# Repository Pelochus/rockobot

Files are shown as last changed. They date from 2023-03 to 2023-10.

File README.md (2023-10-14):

# Rockobot
Battlebot made for SMP subject in Computer Engineering, UGR. This subject focuses on learning microcontrollers and embedded systems, with Arduino especifically. In order to properly learn an actual use case for embedded systems, we have to build a battlebot and make it compete with our classmates' counterparts in a tournament. Personally, we wanted to take the chance to learn a bit more of what was taught in class, so we learned both Fusion 360 and KiCad in order to improve the performance and originality of our robot, adding custom 3D printed parts and a self-designed PCB. Here we have a photo of the final assembly:

RockobotV1

This repository contains information about the mechanics, electronics and programming of the robot along with parts lists, tools used, future ideas and a knowledge database. This README serves as an index for each subsection (Mechanics/Printables, Electronics and Programming) and for some generic stuff. For detailed information, see the READMEs for each subsection:

- [Mechanics/3D Printables](https://github.com/Pelochus/rockobot/tree/main/printables/)
- [Electronics](https://github.com/Pelochus/rockobot/tree/main/electronics/)
- [Arduino/Software](https://github.com/Pelochus/rockobot/tree/main/arduino/)

## Arduino Blog
We were featured in the official Arduino blog! Check this [link](https://blog.arduino.cc/2023/09/29/can-you-smell-what-the-rockobot-is-cooking/)!

## Tournament Results
**Rockobot won 5 matches and tied one!**. Our battlebot achieved the best result of our class, essentially winning the tournament (there were 17 robots including ours, but each one only had to participate in 6 matches). Additionally, we got a 10/10 from our classmates votes. The final mark for Rockobot was a 9.92 out of 10. Here is a video of the full competition:

[Robots Tournament 2023 - SMP UGR](https://www.youtube.com/watch?v=Jcgc2-T2o4o)

# Index
### Mechanics/3D Printables

1. [Components](https://github.com/Pelochus/rockobot/tree/main/printables#Components)
2. [Tools](https://github.com/Pelochus/rockobot/tree/main/printables#Tools)
3. [Requirements](https://github.com/Pelochus/rockobot/tree/main/printables#Requirements)
4. [3D designs](https://github.com/Pelochus/rockobot/tree/main/printables#3D-designs)
5. [Enhancing 3D prints strength](https://github.com/Pelochus/rockobot/tree/main/printables#Enhancing-3D-prints-strength)
6. [Mechanical designs](https://github.com/Pelochus/rockobot/tree/main/printables#Mechanical-designs)
7. [Ideas](https://github.com/Pelochus/rockobot/tree/main/printables#Ideas)
8. [Knowledge Base](https://github.com/Pelochus/rockobot/tree/main/printables#Knowledge-base)

### Electronics

1. [Components](https://github.com/Pelochus/rockobot/tree/main/electronics#Components)
2. [Tools](https://github.com/Pelochus/rockobot/tree/main/electronics#Tools)
3. [PCB](https://github.com/Pelochus/rockobot/tree/main/electronics#PCB)
4. [Circuits](https://github.com/Pelochus/rockobot/tree/main/electronics#Circuits)
5. [Ideas](https://github.com/Pelochus/rockobot/tree/main/electronics#Ideas)
6. [Knowledge Base](https://github.com/Pelochus/rockobot/tree/main/electronics#Knowledge-base)

### Arduino/Software

1. [Components](https://github.com/Pelochus/rockobot/tree/main/arduino#Components)
2. [Tools](https://github.com/Pelochus/rockobot/tree/main/arduino#Tools)
3. [Functions](https://github.com/Pelochus/rockobot/tree/main/arduino#Functions)
4. [Reducing the number of digital pins](https://github.com/Pelochus/rockobot/tree/main/arduino#Reducing-the-number-of-digital-pins)
5. [Ideas](https://github.com/Pelochus/rockobot/tree/main/arduino#Ideas)
6. [Knowledge Base](https://github.com/Pelochus/rockobot/tree/main/arduino#Knowledge-base)

## Why the name Rockobot?
As you can see, Rockobot has Dwayne "The Rock" Johnson head in it. The reason behind this was due to the 3D printing community having a weird obsession with putting The Rock's head on everything they printed and, since we both knew that, we joined our fellow 3D printing enthusiasts in adding The Rock's head everywhere.

## TODO
- Everything is finished! Only need to do a improved version

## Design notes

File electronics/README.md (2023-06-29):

# Electronics 
This section will focus on the electronics side of Rockobot

## Components
| Component | Units | Notes | Link |
| --- | ----- | --- | --- |
| Soldering Tin | - | | - |
| Wires | - | Dupont or common wires | - |
| 5K Ohms Resistors | 4 | Used with infrarred sensors | - |
| 100 Ohms Resistors | 4 | Used with infrarred sensors | - |
| Metallic Power Button | 1 | Red, with LEDs | https://es.aliexpress.com/item/1005004917197015.html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 |
| RCWL-1601 US Sensor | 2 | Very similar to HC-SR04 | https://es.aliexpress.com/item/1005001622236950.html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 |
| TCRT5000 Reflect IR | 4 | | https://es.aliexpress.com/item/32841920225.html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 |
| JGA25-370 DC Motor | 2 | 100RPM@12V **Not used** | |
| L289N Motor Driver | 1 | | https://es.aliexpress.com/item/33012645746.html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 |
| StepDown Converter 5V | 2 | One at ~8V the other at ~5V | https://es.aliexpress.com/item/1005003709975604.html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 |
| 1550mAh 14.8V Battery | 1 | 4S LiPo, with XT60 connector  | https://www.amazon.es/Tattu-Batería-Multicopteros-Helicópteros-diversos/dp/B016Q3QT2W/ref=sr_1_6?__mk_es_ES=ÅMÅŽÕÑ&crid=17YJJHHE4X53W&keywords=bateria+4s+lipo&qid=1688040709&sprefix=bateria+4s+lipo+%2Caps%2C218&sr=8-6 |
| Battery Alarm | 1 | | https://es.aliexpress.com/item/1005003884877902.html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 |
| XT-60 Female | 1 | Used for battery connection | https://es.aliexpress.com/item/32832063718.html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 |
| JSTXH2.54 4P Wire | 6 | For sensors/motors connection | https://es.aliexpress.com/item/32954418743.html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 |
| JSTXH2.54 4P Female | 6 | For sensors/motors connection | Link above |
| Male 2.54 Pins | ~20 | For some connections/upgrades | https://es.aliexpress.com/item/32864964634.html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 |
| Rockobot v1.0 PCB | 1 | | |
| Optional Components | - | Some other useful components: | Heat Shrink tubing, insulating tape... |

## Tools
- Soldering Iron
- Balance Charger

## PCB
Here we have a photo of the PCB in KiCad:

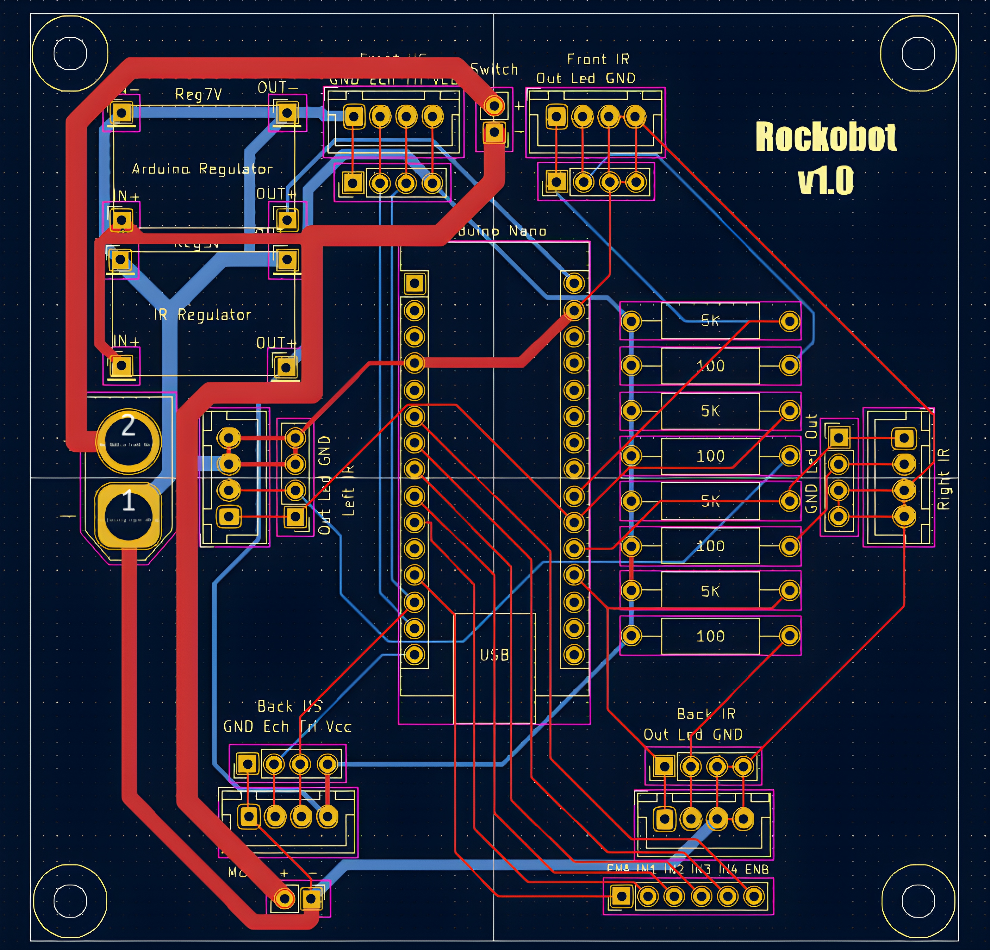
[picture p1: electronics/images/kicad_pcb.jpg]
KiCadPCB


We can see these components:
- Various connectors, including male 2.54 pins, JSTXH 2.54 for the sensors and XT60 male for the battery
- Resistors for the IR sensors
- 2 voltage regulators, one will be exclusively for the Arduino (needs more than 7V, max 12V, the Vin pin will do the rest) and the other for the sensors (both infrarred and US) at 5 volts
- Arduino NANO itself

The final result should look like this (except for all the male pins which are connected to the JST, which are **backup connectors**):

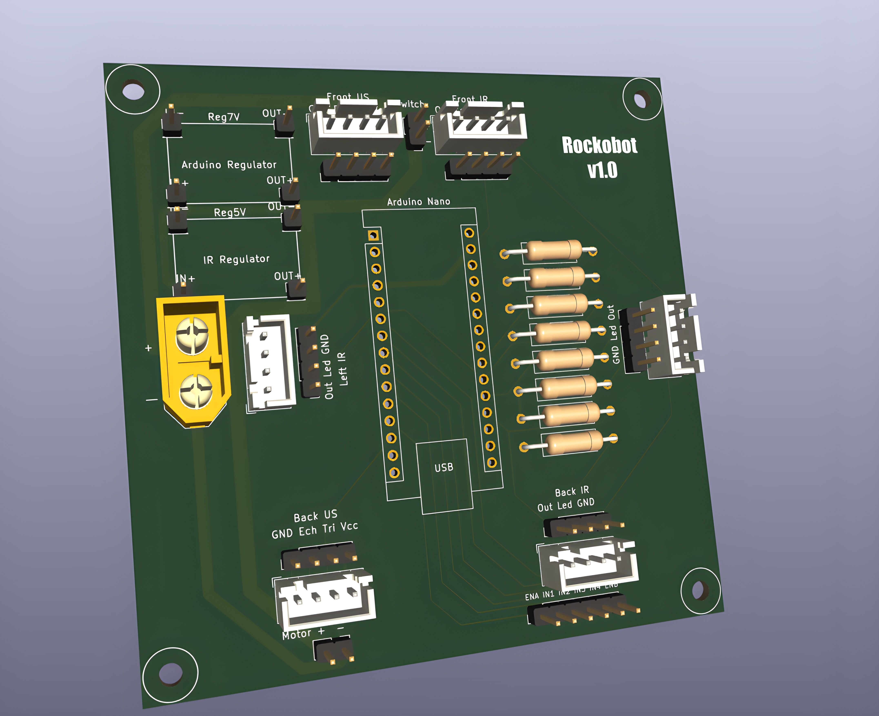
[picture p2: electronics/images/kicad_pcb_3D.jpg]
KiCadPCB3D


However we made little changes to adapt it to our final design. The only two important changes are **the female pins for the Arduino** (so we can remove it or insert it whenever we want) and the **position of the XT60 connector**, which is facing downwards because our battery didn't have a long enough wire. We also did not include those extra male pins, which were inserted just in case we had problems with the JST connectors.

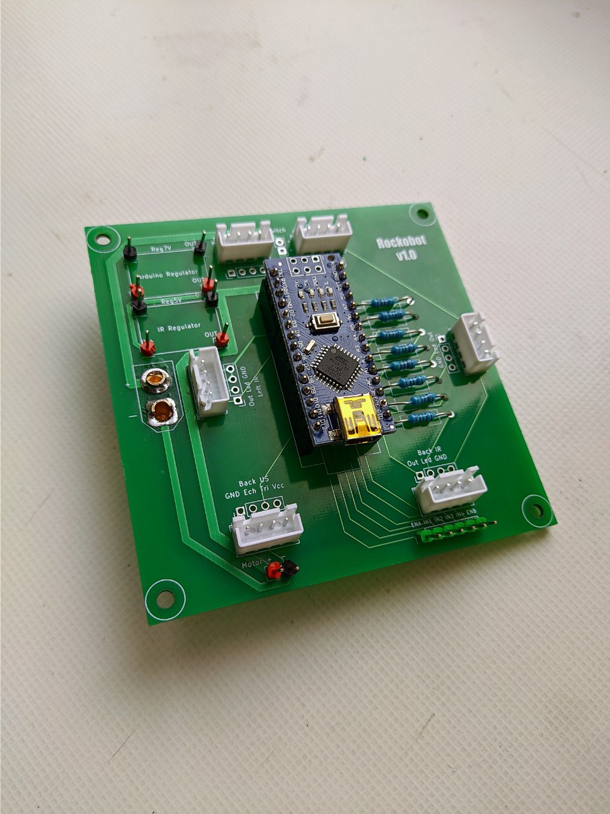
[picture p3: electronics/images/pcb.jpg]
PCB-Almost-Finished


Here is the totally finished design integrated in the robot (we used insulating tape to avoid unintended shortcircuits):

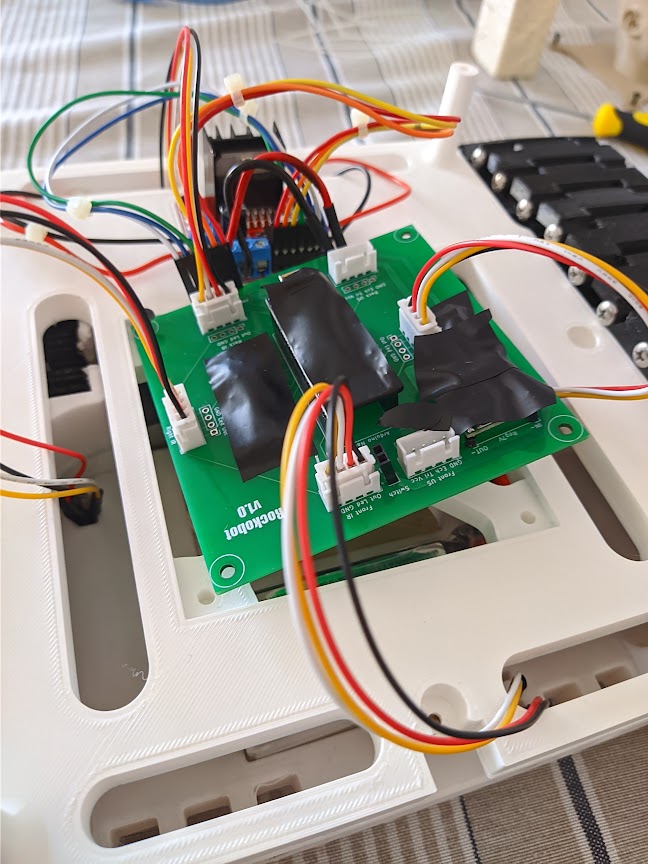
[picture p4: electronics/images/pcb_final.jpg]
PCB-Finished


## Circuits
This is a photo of the schematic:

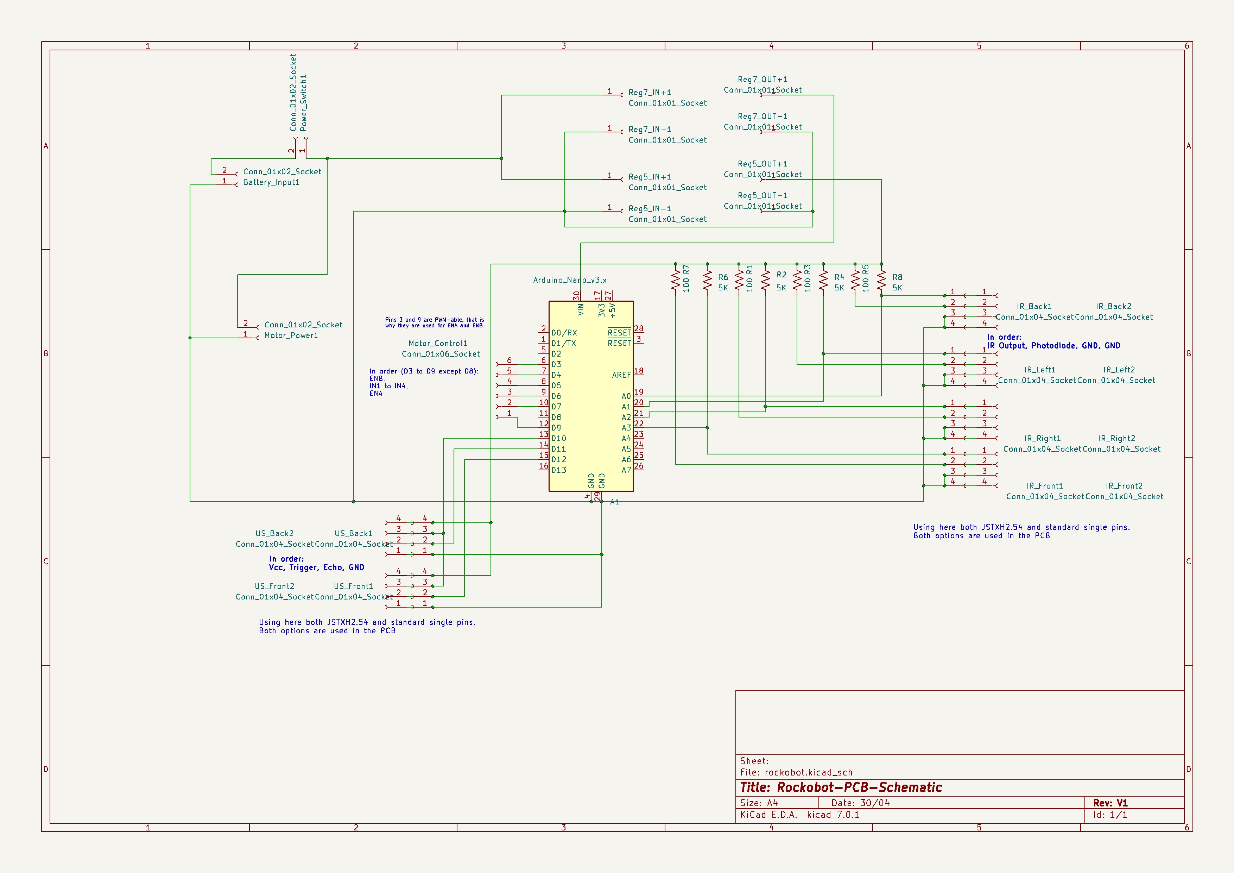
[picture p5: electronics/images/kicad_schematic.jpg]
KiCadSchematic


Essentially, the circuit does this:

Connection to battery -> Power Button -> Divide current in 3, one directly to the L298N driver, the other 2 to the voltage regulators -> One regulator will power the Arduino through V<sub>in</sub>, the other will power the sensors -> Connect Arduino and sensors/driver through digital pins and analog pins

## Ideas
Here are some ideas for future revisions:
- Change from Arduino NANO to, for example, ESP32
- Add a section to the PCB with male pins connected to the digital pins, to add some modularity. Also add two more male pins, one connected to Arduino 5V and the other to GND
- Change some pins (like the 6 motor driver pins) to other JST XH2.54 or other connectors. For the previous example, from common male pins to JST XH2.54 6P
- Rethink some components like the regulators. For example:
  - Reduce to just one regulator, by using the Arduino for powering sensors (depending on how many sensors are used, in this design it is possible but near the Arduino limit)
  - Change to a fixed SMD regulator, to avoid changing the potentiometer unintentionally to an unsafe voltage. Also to better fit in the PCB (current implementation is rather messy)
- Resize PCB accordingly to what new changes were introduced

## Knowledge Base
- [KiCad 7 Tutorial, from schematics to final PCB](https://www.youtube.com/watch?v=3FGNw28xBr0)

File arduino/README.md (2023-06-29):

# Software
This section will focus on the software side of Rockobot

## Components
- Arduino NANO V3 or clone. We used Elegoo NANO V3

## Tools
- Computer
- Mini USB-B to USB-A/USB-C
- Arduino IDE

## Functions
The majority of functions here are very simple, except for the main function that decides what to do. There is information about the library for controlling the motor driver [here](https://github.com/Pelochus/rockobot/blob/main/arduino/libraries/l298n-rockobot/README.md). Let's take a look at the main function of Rockobot:
```c++
void rockobot_think() {
  extra_delay = 800; // Add an extra delay when encountering black lines

  ////////////////
  // Read Sensors
  ////////////////
  uint8_t front_distance = us_front.measureDistanceCm();
  uint8_t back_distance = us_back.measureDistanceCm();
  bool ir_front = (analogRead(IR_FRONT) > IR_THRESHOLD);
  bool ir_back = (analogRead(IR_BACK) > IR_THRESHOLD);
  bool ir_right = (analogRead(IR_RIGHT) > IR_THRESHOLD);
  bool ir_left = (analogRead(IR_LEFT) > IR_THRESHOLD);

  /////////
  // Think
  /////////
  uint8_t speed = 100;
  direction_t direction = driver.get_direction(); // Maintain same path while thinking

  // Anti-ramp
  if ((ir_front ? 1 : 0) + (ir_back ? 1 : 0) +
      (ir_right ? 1 : 0) + (ir_left ? 1 : 0) > 2) {
    direction = RIGHT;
  }
  else if (ir_front) {
    direction = BACKWARD;
  }

  /**
   * Rest of IR ifs
   */

  // We want even higher delays on rotations, because robot is slower with only one motor
  else if (ir_right) {
    extra_delay += 200;
    direction = WIDE_LEFT;
  }
  else {
    ///////////////////////////////////////////////////////
    // Not in danger zone, search and target enemy with US
    ///////////////////////////////////////////////////////
    extra_delay = 0; // Reset delay if not in danger
    speed = 80;

    int16_t us_diff = front_distance - back_distance; // If negative, back_distance is farther from something and viceversa
    uint8_t us_min = (front_distance < back_distance) ? front_distance : back_distance;
    bool search = us_min > US_NEARBY_ENEMY; // Decide whether to skip or not search stage

    //////////
    // Search
    //////////

    if (search) {
      switch (search_stage) {
        case 0 ... (TURN_CYCLES - 1):
          direction = RIGHT;
          break;
        case 2 * TURN_CYCLES ... (3 * TURN_CYCLES):
          direction = LEFT;
          break;
        default:
          direction = FORWARD;
      }

      search_stage++;
      search_stage %= 4 * TURN_CYCLES;
    }

    ////////////////
    // Target enemy
    ////////////////

    if (abs(us_diff) > DIRECTION_CHANGE_THRESHOLD && us_min < US_NEARBY_ENEMY) {
      if (us_diff > 0) direction = BACKWARD;
      else if (us_diff < 0) direction = FORWARD;
      // else will retain current direction
    }

    // Activate max power if close enough
    if (us_min < FULL_POWER_NEAR_ENEMY) speed = 100;
  }

  //////////////////////
  // Act after thinking
  //////////////////////

  driver.set_speed_percentage(speed);
  driver.set_direction(direction);
}
```

As we can see, we can easily divide the function in 3 parts: **sense, think and act**

We have some extra functionality to the robot, like the ```extra_delay``` variable, which augments the delay between one loop and the following when encountering black lines. This way, we do not allow the robot to rethink actions very frequently while it is avoiding black lines, just escapes from the black lines. Some of this extra functionality is outside the main function and is implemented either on the ```void setup()``` or the ```void loop()```. For extra details on the main function, see [rockobot-main.ino](https://github.com/Pelochus/rockobot/blob/main/arduino/rockobot-main/rockobot-main.ino)

## Reducing the number of digital pins
Since an Arduino NANO only has 13 digital pins, controlling 2 US sensors, 4 infrarred sensors and 2 motors is almost impossible without using transistors or other methods of switching elements.
Luckily, since we have some redundancy, we can "compress" the number of pins used. First, let's see how many pins we need:

- **2 digital pins** for each ultrasonic sensor, so **4 in total**
- **1 digital pin** per infrarred sensor, **4 in total**
- **4 analogic pins**, 1 per infrarred sensor
- **6 digital pins** (2 must be PWM) for the motor driver

As we can see, **14 digital pins**, 1 more than what a Nano has. We reduced the pins the following way:

- **3 digital pins** for the US sensors, we used the same pin for the trigger pin of each one, since we will mostly reading both at once
- **0 digital pins** for the infrarred sensors, changed for 5V pin. This was necessary for the infrarred LED to be turned on or off, but we can keep it on indefinitely
- The driver **could be using 5 pins** (combine the digital pin used for PWM), but we will keep them separately just in case we want to have different speeds per motor

With this reduction, **we only use 9 digital pins**, having some spare digital pins in case we wanted to add, for example, bumpers or decorative LEDs.

## Ideas
- Switch between IR controlled mode and autonomous mode:
    - Wait for an input at setup with 2 buttons, one for each mode, in loop function, call either autonomous or controlled mode
    - Make the input a key, similar to a car

## Knowledge Base
- [Arduino Docs](https://docs.arduino.cc/)
- [UltraSonic Sensor Library](https://github.com/Martinsos/arduino-lib-hc-sr04)

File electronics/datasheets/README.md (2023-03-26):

# Datasheets
This subsections is of minor importance. Below some notes about the datasheets of the electronic components used

## Notes
- RCWL-1601 ultrasonic sensor is extremely similar to HC-SR04 counterpart but better. Almost everything is equal (even software) except for lower consumption (2 mA vs 8 mA) and this sensor is capable of 3.3V logic, making it a better choice for RPi and ESP32
- There is no specific datasheet for the 12V@100 RPM edition of the JGA25-370, so a partially complete datasheet + some PNGs from the store it was bought are included
- The step-down converter does not even have a specific part number. Similarly, some screenshots are included with information
- The red metallic button is also generic, so again some screenshots with some specs

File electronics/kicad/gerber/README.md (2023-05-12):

## Note about gerber files
Gerber files here are generated for JLCPCB according to their guide for KiCad 6/7. The .zip contains all files necessary for ordering

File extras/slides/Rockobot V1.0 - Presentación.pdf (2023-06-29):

# Rockobot V1.0

# Realizado por:

# Ángel Hurtado José Hinojosa

# Índice

## - Objetivos

## - Diseño 3D:

## - Estructura

## - Mecánica

## - Electrónica

## - Componentes

## - PCB

## - Programación

## - Problemas

# Objetivos

## Queríamos hacer un robot que cumpliese lo siguiente:

## - Fuerte y grande

## - Modular y reparable

## - Impreso en 3D en su mayoría

## - Usar Orugas (Tanque)

## - Circuitería ordenada

## - Programación simple

# Diseño 3D: Estructura

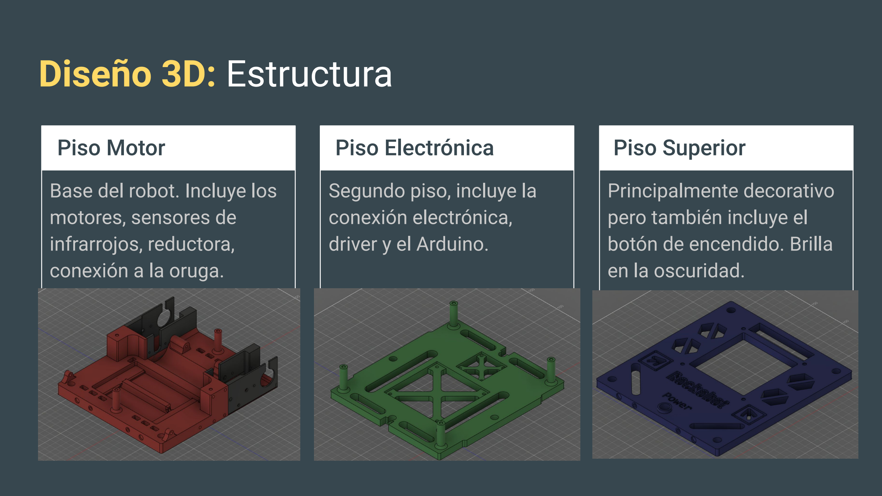
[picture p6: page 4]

## Piso Motor

### Base del robot. Incluye los motores, sensores de

infrarrojos, reductora,
conexión a la oruga.

## Piso Electrónica

### Segundo piso, incluye la

conexión electrónica,
driver y el Arduino.

## Piso Superior

### Principalmente decorativo pero también incluye el botón de encendido. Brilla

en la oscuridad.

# Diseño 3D: Estructura

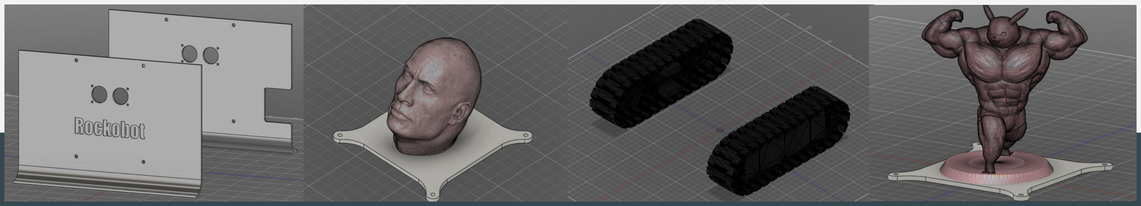
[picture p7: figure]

## Shields

Escudos de acero
inoxidable. Integran en
ellos unos agujeros para el sensor de ultrasonidos

## Rockins

Módulos para el piso
superior. Principalmente
decorativos, pero pueden
ser funcionales
(iluminación, por ejemplo)

## Tracks

4 piezas: Oruga de plástico flexible, frame para
conexión oruga-cuerpo y 2
tipos de engranajes: para
movimiento y para tensión

## Otros componentes

Para conexión de las
piezas se usaron tornillos, tuercas, threaded inserts, arandelas, silicona para
algunos apaños etc...

# Diseño 3D: Mecánica

## - 3 partes:

- Caja de engranajes
- Oruga con filamento flexible (TPU)
- Frame para la oruga y conexión con engranajes

## - Lubricación de engranajes con vaselina (el plástico para impresoras 3D lo prefiere a otros lubricantes) - Muchos tornillos (unos 120, 64 para la oruga) - Reducción de velocidad aproximadamente 86:1 (86 veces más lento, pero mayor par motor)

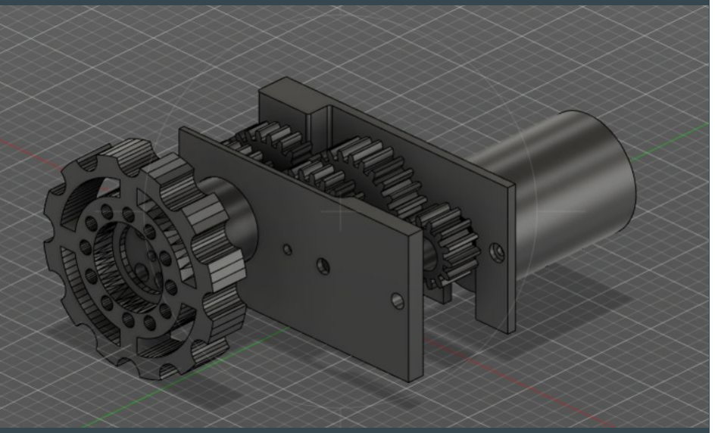
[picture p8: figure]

Gearbox, motor y engranaje principal, que engancha a la oruga flexible

# Construcción del diseño 3D

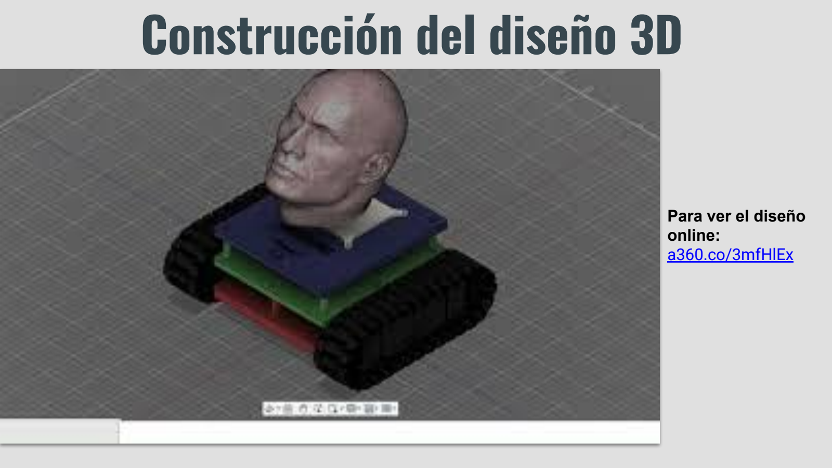
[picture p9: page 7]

Para ver el diseño
online:
a360.co/3mfHlEx

# Electrónica: Componentes

Componentes usados:

- Arduino NANO v3
- L298N motor driver
- RCWL-1601 US sensor x2
- TCRT5000 IR sensor x4
- Step-Down converter Mini 360 x2
- Batería de 14.8V y 1550 mAh
- Alarma para batería baja
- Motores de un VHS antiguo x2
- Rockobot V1.0 PCB
- Botón guay de Aliexpress
- Conector XT-60 (para batería)
- Conectores y cables JSTXH2.5, para los sensores
- Resistencias, cables, estaño…

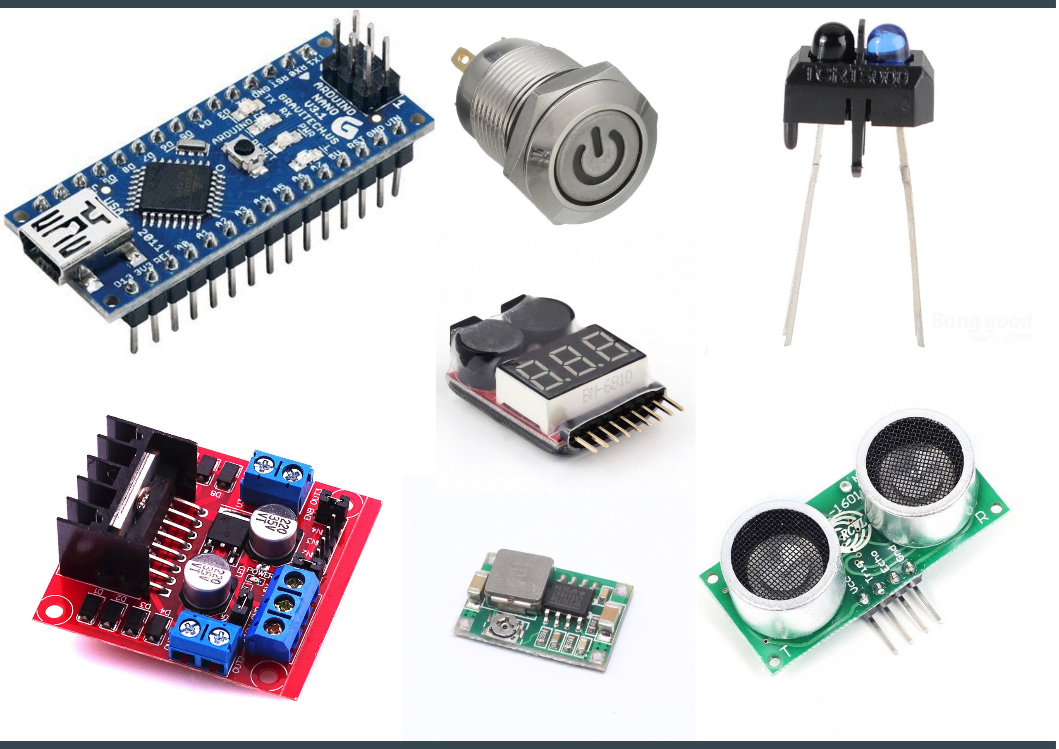
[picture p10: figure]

Electrónica: Componentes | Esquema electrónico del
robot. Se divide tal que: - Entrada de la batería

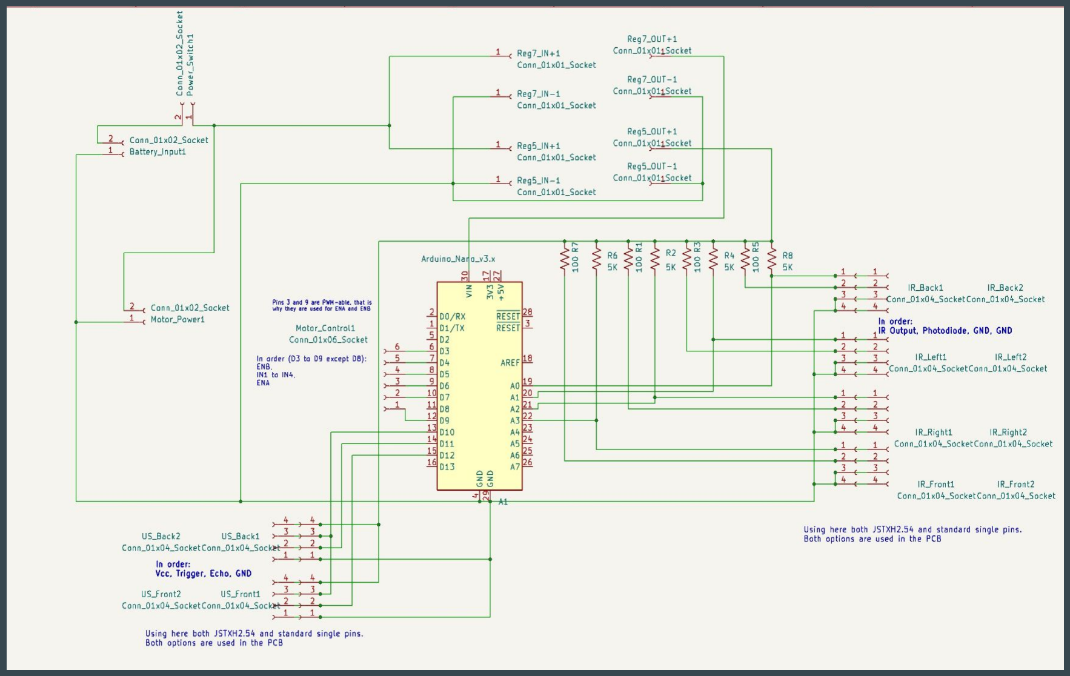
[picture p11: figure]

| - Botón de encendido
| - Conexión a reguladores de voltaje
- Regulador 1 alimenta
sensores de IR y
sensores de US a ~5.1V
- Regulador 2 alimenta el
Arduino mediante pin
Vin a unos ~7.5V (el
regulador interno reduce
a 5V)
- Conexión de pines del
Arduino a sensores y
driver
- Alimentación directa de
la batería al driver de
motor

# Electrónica: PCB

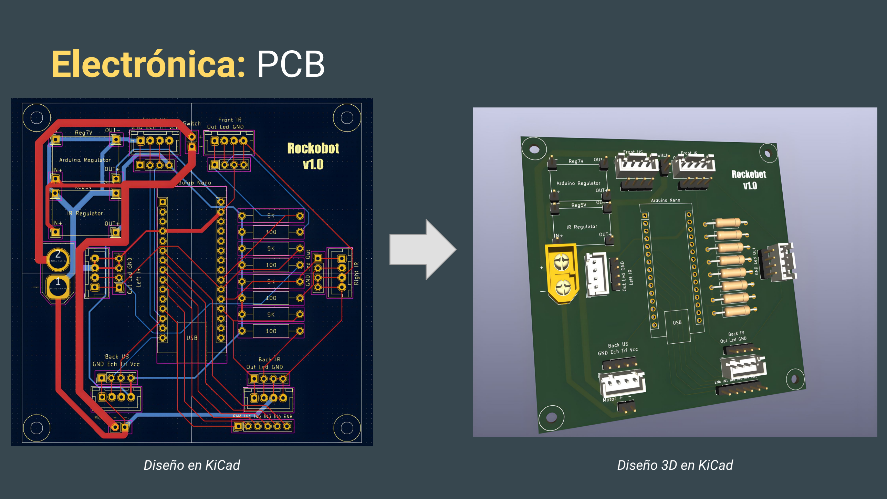
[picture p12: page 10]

Diseño en KiCad | Diseño 3D en KiCad

# Electrónica: PCB

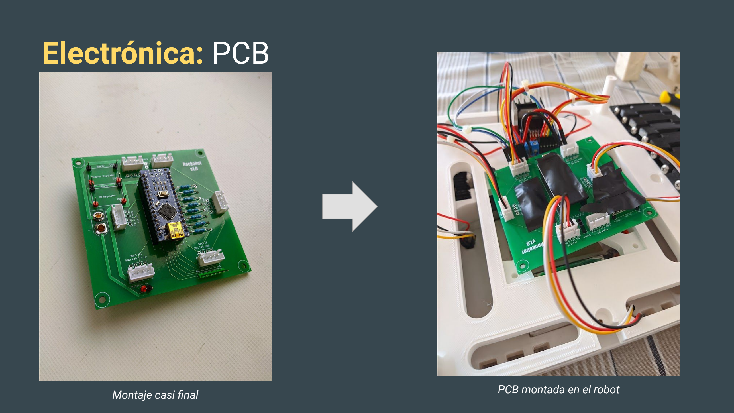
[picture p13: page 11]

Montaje casi final | PCB montada en el robot

# Probando la fuerza del motor

# Programación

## Sensores

- Ultrasonidos: librería para HC-SR04, funciona con el sensor que usamos perfectamente.
- IR reflexivo: Solo hay que usar analogRead()

## Arduino

- Recibe señales de los sensores, procesa la información y decide en un conjunto de if, si avanzar, girar, retroceder, cambiar la velocidad… cada 50 ms. Controla el driver

## L298N Driver

- Alimentación directa de la batería, conexión con Arduino mediante 6 pines (4 para puente H, 2 para PWM)
- Controla ambos motores mediante librería propia
Motores | ● | Reciben el voltaje del driver, variable según PWM y batería restante. Se mueven a unas 20-80 RPM

# Programación

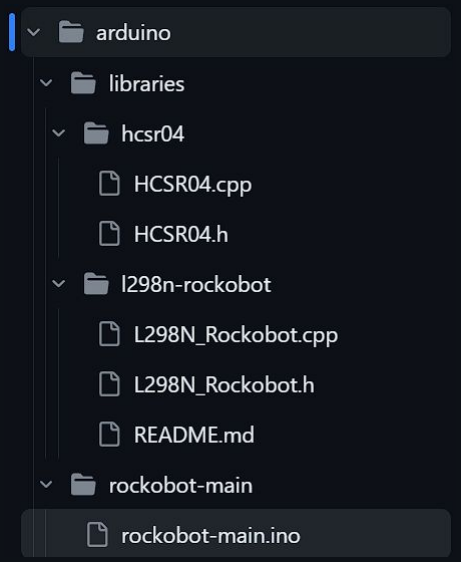
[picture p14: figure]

Estructura de ficheros para programar el Arduino

La programación incluye los siguientes ficheros

- HCSR04.cpp: Librería extraída de GitHub

para control fácil del sensor de ultrasonidos.

Funciona con nuestro modelo de ultrasonidos

- L298N_Rockobot.cpp: Librería propia para

el control de motores. Incluye una pequeña

clase y enumerados para indicar fácilmente si

se quiere girar, avanzar, retroceder, a qué

velocidad, saber velocidad, rotación actual…

- rockobot-main.ino: Archivo principal,

incluye las constantes, librerías previas, código

principal… Se divide en 3 partes:

- Leer de sensores
- Decidir
- Enviar a motores

# Problemas

Lista de problemas que sufrimos:
- Cortocircuito de un Arduino
- Problemas a la hora de imprimir, tanto José como Ángel
- Atasco en la boquilla de la impresora de Ángel
- Rotura de una pieza en medio de una impresión (Ángel también)
- La pieza más grande (300 gramos) tuvo un problema de impresión (José)
- El montaje, tanto de los motores, como la oruga, como de un piso a otro…
- Los malditos ejes de la reductora (salían y se doblaban)
- En una ocasión se nos fusionaron 2 engranajes de la reductora con el eje. Esto se debió al roce entre un engranaje y el otro. El PLA técnicamente empieza a derretirse a los 50-60ºC, pero creemos que llegó a más.
- El diseño 3D tomó mucho tiempo, es más, el diseño actual tiene cambios que no tienen las piezas impresas del robot, tuvimos que hacer adaptaciones con silicona y (des)soldando plástico. Hay cerca de 700 dimensiones en el robot.

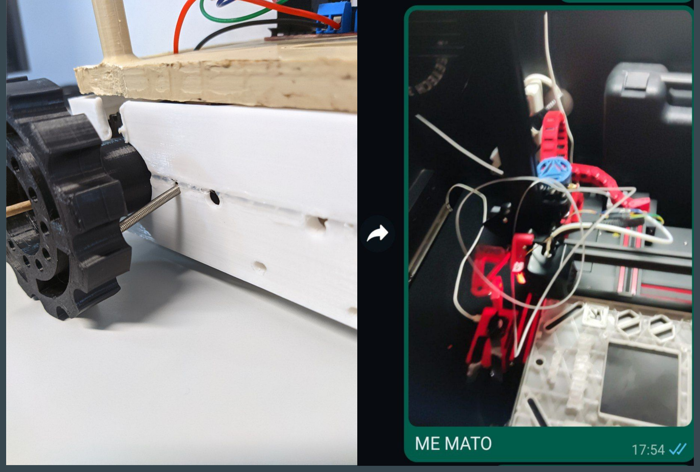
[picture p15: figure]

Varilla doblada (izquierda), impresora se le sale el tubo en medio de impresión (derecha) y pieza de 300 g (24 horas de impresión) se salta capas de impresión (abajo)

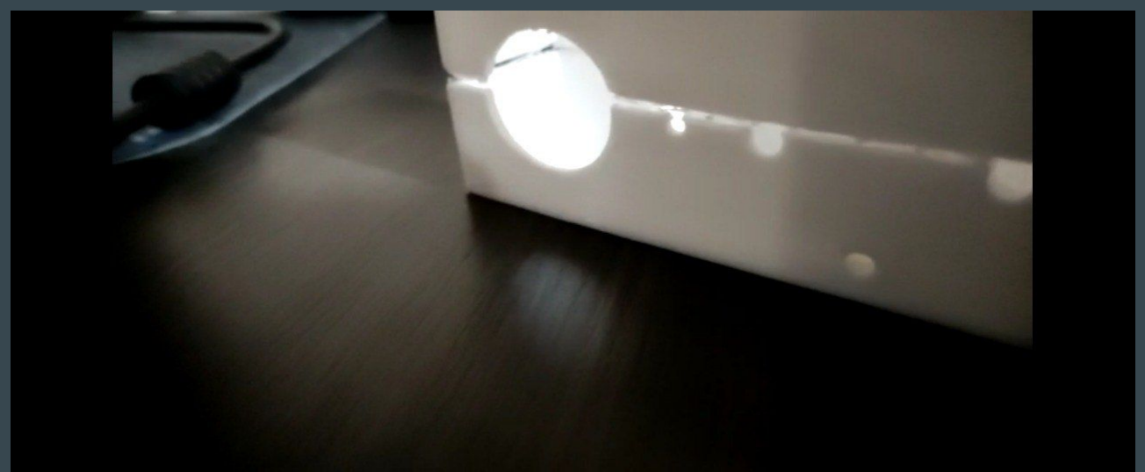
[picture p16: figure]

# ¿Github? Sí

# github.com/Pelochus/rockobot

# Incluimos diseños 3D, diseño electrónico, código, archivos para imprimir, consejos para imprimir piezas resistentes, explicación de la mecánica, datasheets de los componentes

electrónicos, listas de componentes, explicación de la librería para el driver, ideas para

# mejorar el robot, instrucciones para crear el escudo de acero, esta presentación…

# ¿Instrucciones de montaje? No

# Ni siquiera nosotros sabemos montarlo bien

# Fin

# Gracias

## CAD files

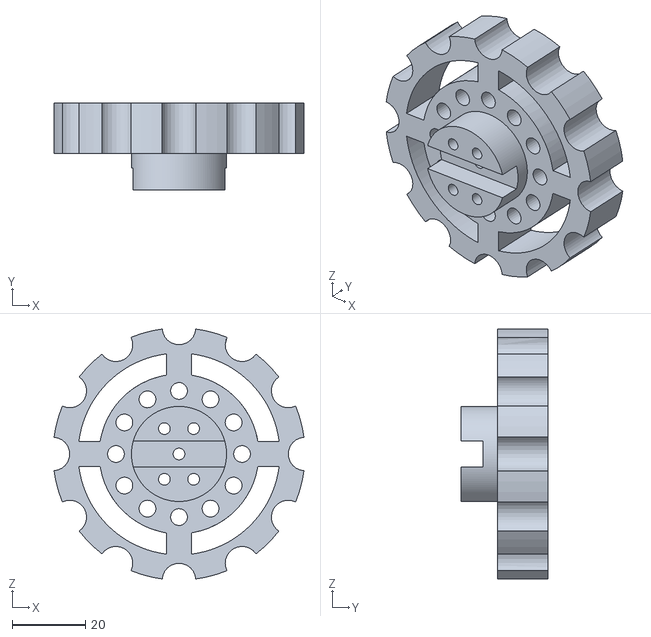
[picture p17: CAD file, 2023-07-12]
printables/stl/gearbox/MainCog.stl
68.4 x 23.8 x 68.4

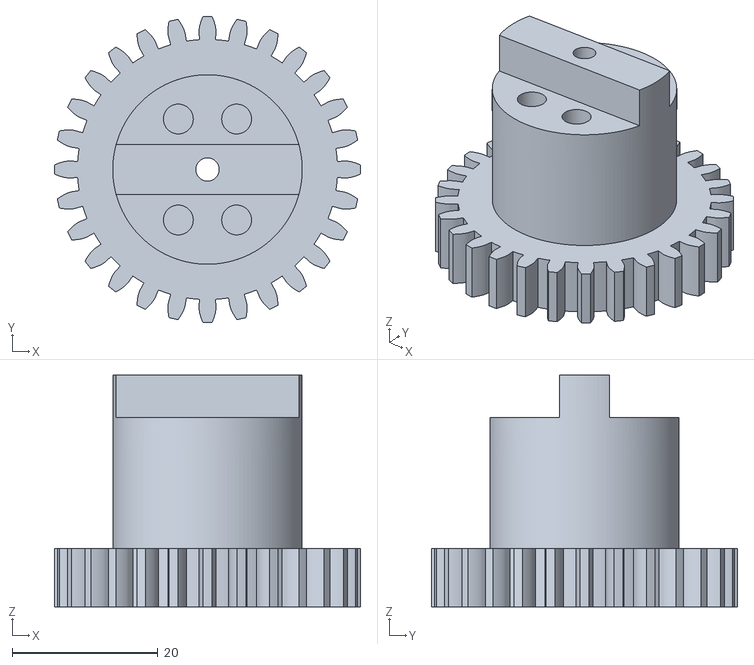
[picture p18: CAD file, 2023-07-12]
printables/stl/gearbox/MainCogGear.stl
42.0 x 42.0 x 31.8

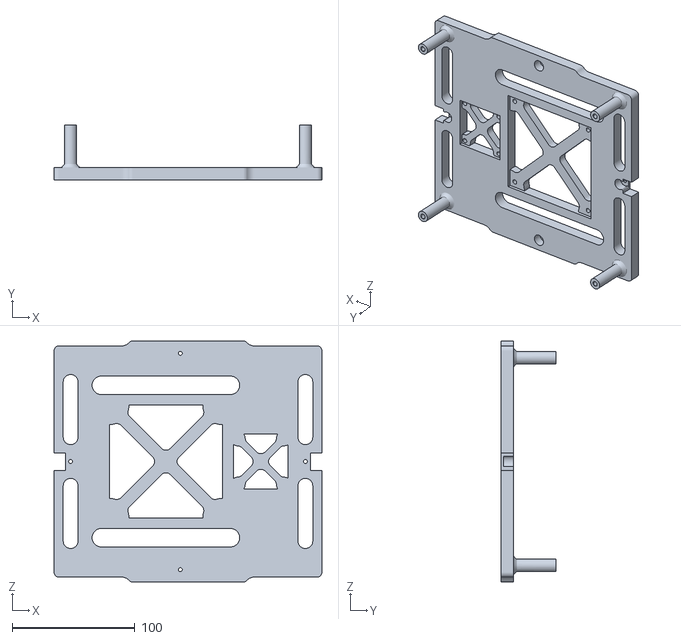
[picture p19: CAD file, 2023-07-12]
printables/stl/core/ElectronicsFloor.stl
218.0 x 44.5 x 196.0

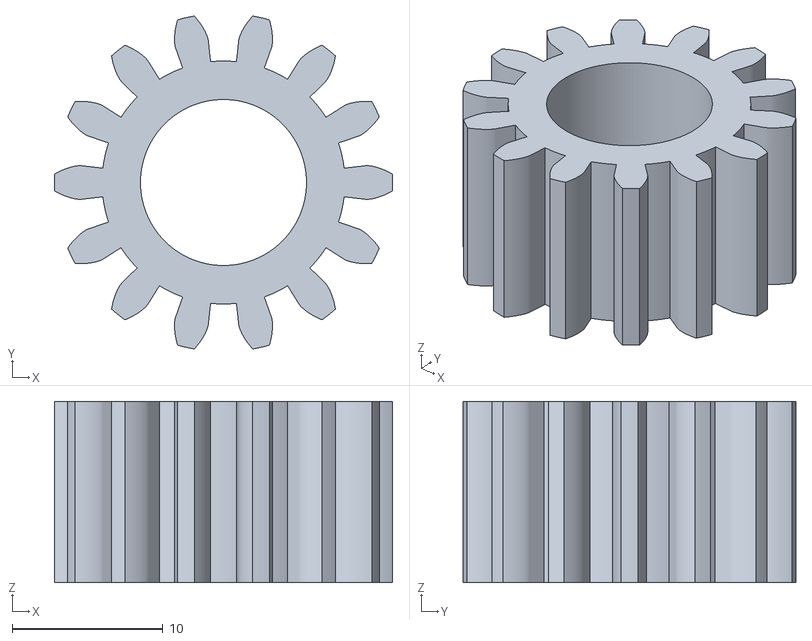
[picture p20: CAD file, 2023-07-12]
printables/stl/gearbox/MotorGear.stl
22.4 x 22.1 x 12.0

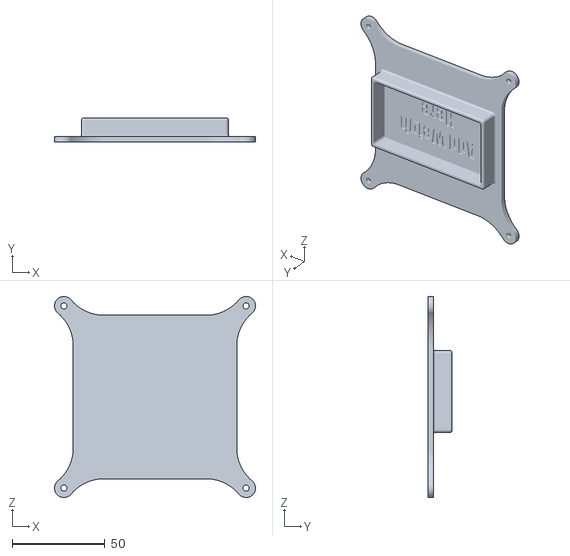
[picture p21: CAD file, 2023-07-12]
printables/stl/rockins/Rockin-Weigh.stl
108.1 x 13.0 x 108.1

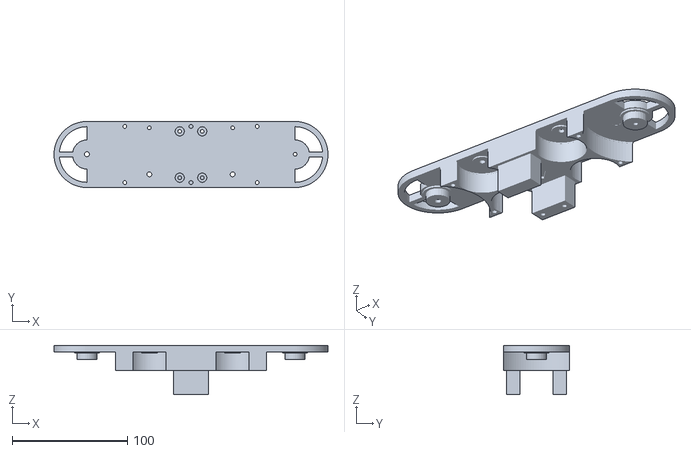
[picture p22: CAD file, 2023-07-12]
printables/stl/tracks/OuterConnectorLeft.stl
238.2 x 57.5 x 43.0

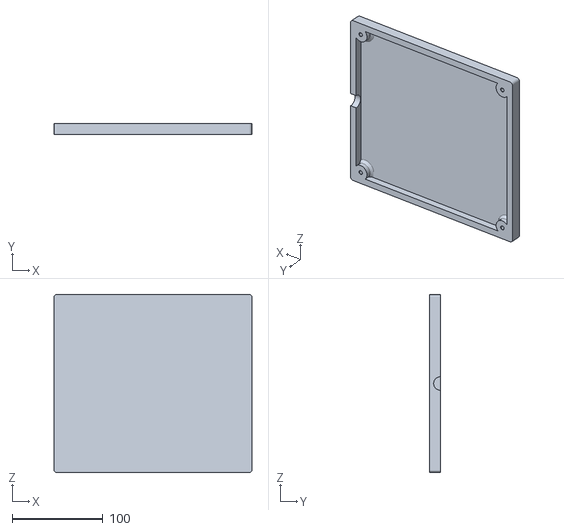
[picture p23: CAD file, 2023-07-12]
printables/stl/core/FillableBase.stl
218.0 x 12.0 x 196.0

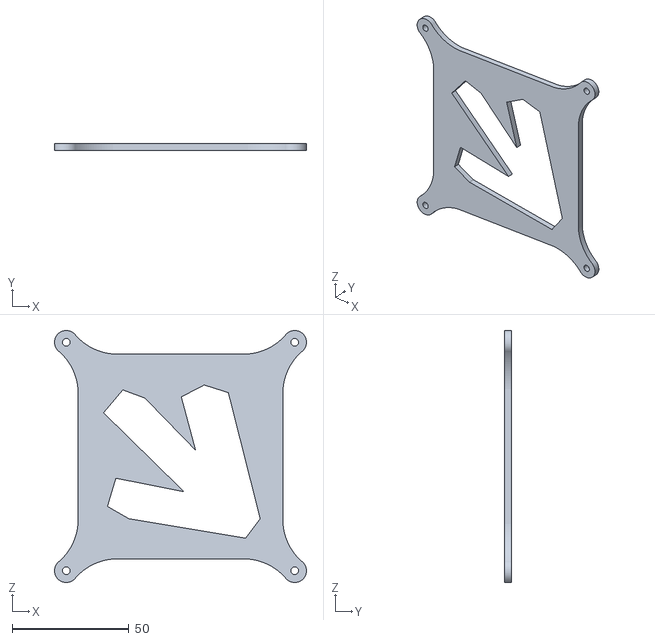
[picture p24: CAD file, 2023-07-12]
printables/stl/rockins/Rockin-SWAD.stl
108.1 x 3.00 x 108.1

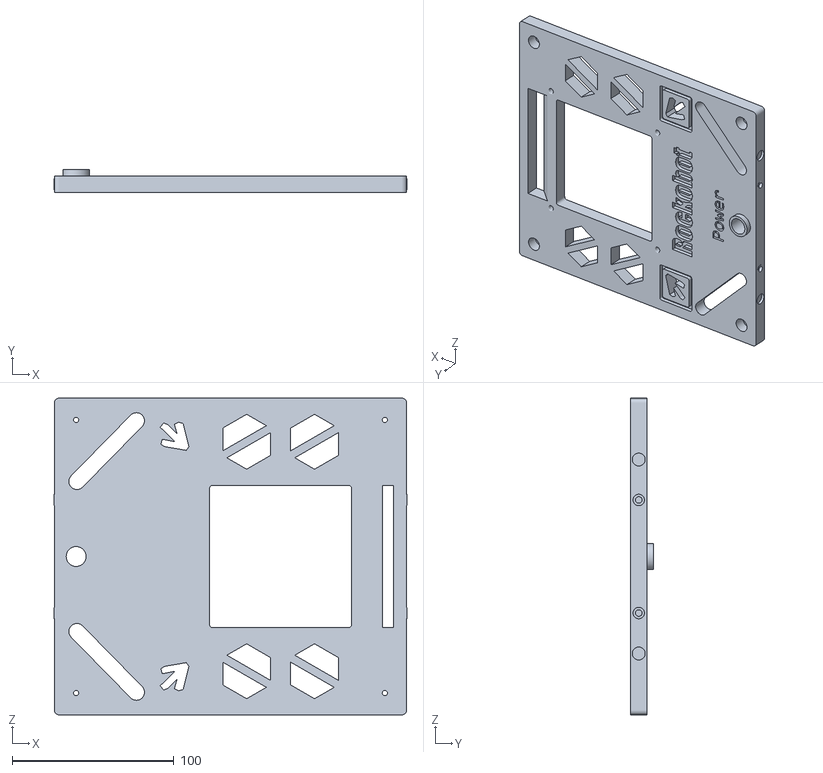
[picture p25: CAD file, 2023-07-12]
printables/stl/core/TopLayer.stl
218.4 x 14.0 x 196.0

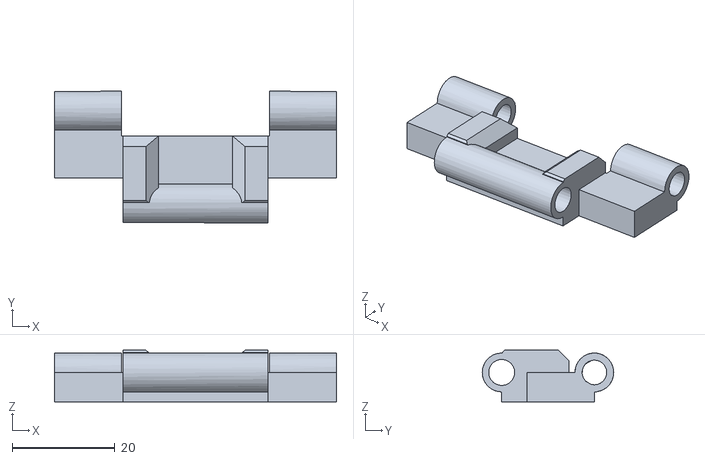
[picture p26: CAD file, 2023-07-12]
printables/stl/tracks/SingleTrack.stl
55.0 x 25.7 x 10.1

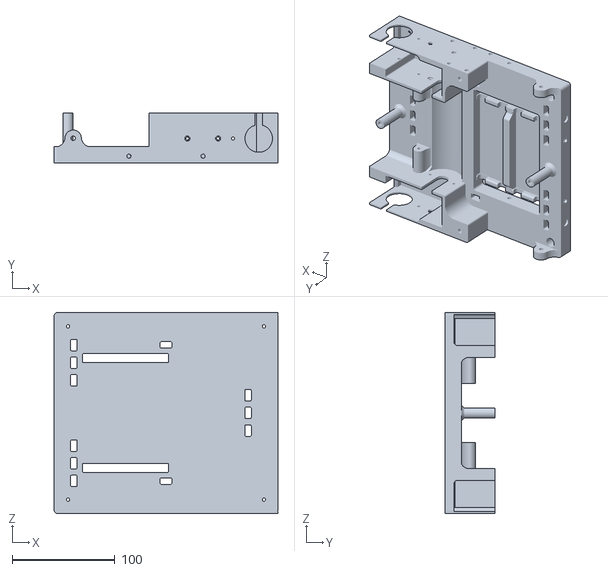
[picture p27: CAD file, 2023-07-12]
printables/stl/core/MotorsFloor.stl
218.4 x 49.0 x 196.0

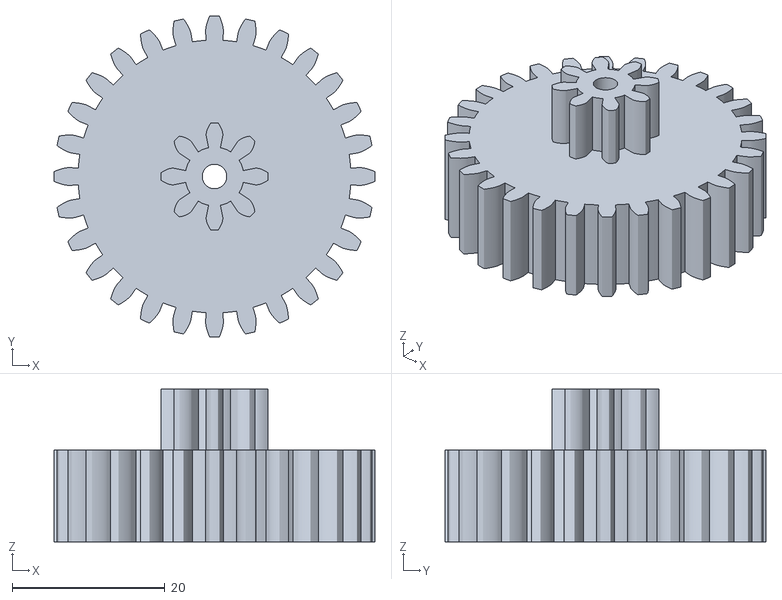
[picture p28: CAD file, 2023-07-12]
printables/stl/gearbox/Gear1.stl
42.0 x 42.0 x 20.0

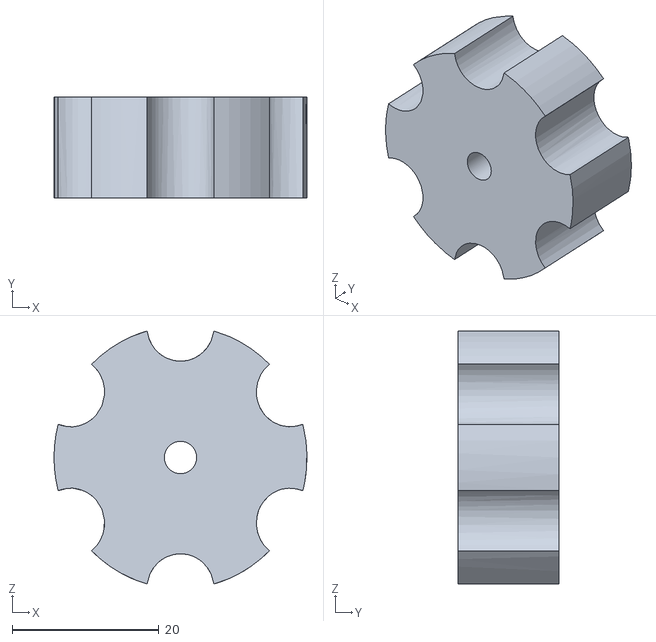
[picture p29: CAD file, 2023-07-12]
printables/stl/tracks/LowerSmallCog.stl
34.5 x 13.8 x 34.5

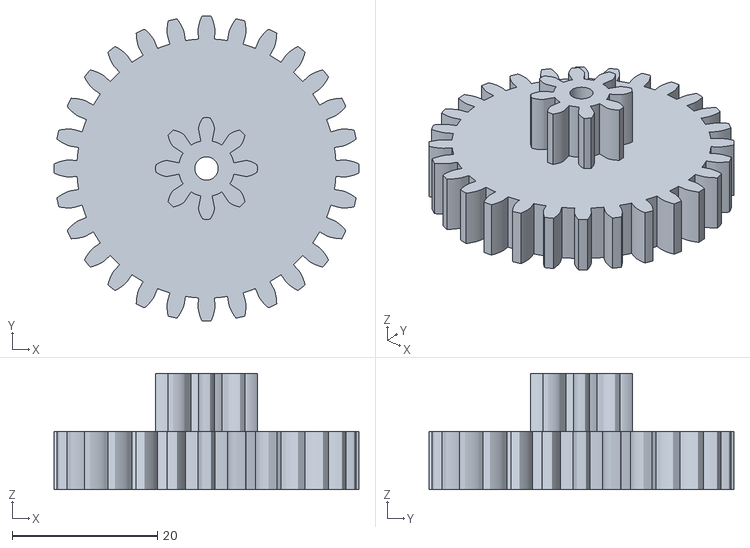
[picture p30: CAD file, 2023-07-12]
printables/stl/gearbox/Gear2.stl
42.0 x 42.0 x 16.0

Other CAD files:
printables/stl/tracks/OuterConnectorRight.stl
printables/stl/tracks/UpperSmallCog.stl
printables/fusion360/Rockin-Base.f3d

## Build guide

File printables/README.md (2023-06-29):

# Printables and Mechanics
This section will focus on the printables and mechanics sides of Rockobot<br>
If you want the STLs files or CAD files click this [link for STLs](https://github.com/Pelochus/rockobot/tree/main/printables/stl) or this [one for Fusion 360 files](https://github.com/Pelochus/rockobot/tree/main/printables/fusion360)

## Components

| Component | Units | Notes |
| --- | ----- | --- |
| Motor | 2 | Extracted from old VHS |
| PLA/PLA+ | 850 g | Weight is estimated |
| TPU 95A | 250 g | Weight is estimated |
| M3x8 Screws | 32 | |
| M3x20 Screws | 20 | |
| M4x60 Screws | 70 | Used in tracks and some cogs |
| M4 Stop Nuts | 64 | Used along the M4 screws |
| M3 Threaded Insert | 50 | Ruthex Brand |
| M3x80 Rod | 4 | If threaded, use x8 M3 stop nuts |
| M3 Nuts | ~15 | Used with threaded rods |
| M4 Nuts | ~8 | Used with some OutConn screws |
| Optional components | - | Vaseline (lubricant), washers, silicone... |

## Tools
- Screwdrivers
- Soldering Iron (inserting threaded inserts in prints)
- 3D printers (we used these):
    - Ender 3 V2
    - Elegoo Neptune 2

## Requirements
- Get as close as possible to the 4 kg limit
- Make it near as big as the limit (350x350 mm)
- Low center of gravity, high stability
- Good traction, no slippery wheels
- High Torque, speed is not important
- High resistance parts, intelligently print parts as durable as possible (high temps, low speeds, better materials, intelligent designs)
- Intelligently design parts for durability

## 3D designs
### Rockobot Core
Here is a photo of the full design in Fusion 360. This only includes what was designed with Fusion, not any other mechanical component. There may be some minor differences, since the mounted has some manual adaptations that were later introduced properly to the design.

**You can easily inspect the full design [here](https://a360.co/3mfHlEx)**

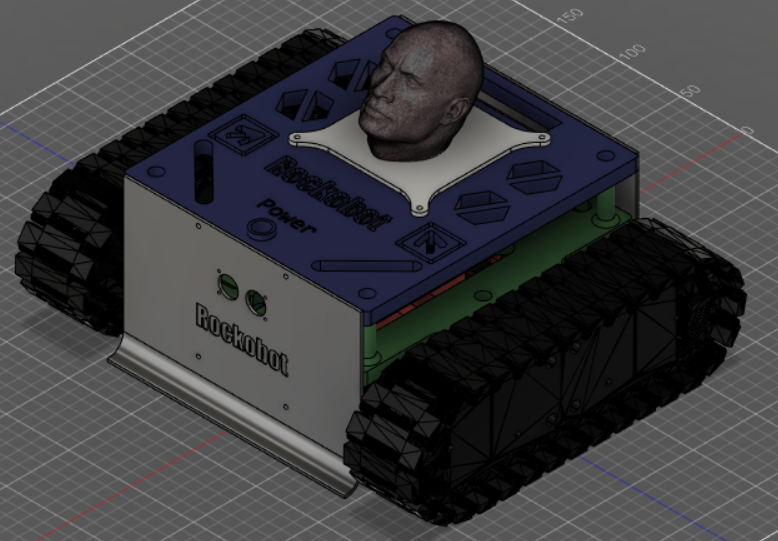
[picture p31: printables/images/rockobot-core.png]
Full-Design


#### Fillable Base
This was not used in final design, but its purpose was being filled with something dense and liquid/fluid so that the robot weigh could be changed easily.
Our idea was to use sand, but it isn't a great idea mixing 3D prints (which are not totally sealed, due to the concept of layers) with something like sand. Also added complications with the infrarred sensors, so it was abandoned as an idea, but still present in the design.

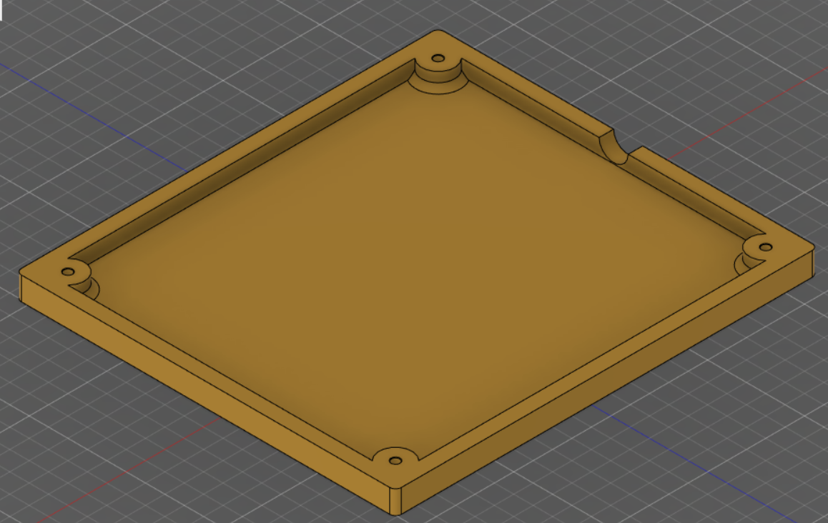
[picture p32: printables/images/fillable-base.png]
Fillable-Base


#### Motors Floor
Biggest, most important 3D printed part of the whole design. Will need at least 280 g of plastic. The purpose of this floor is to connect the motor to the tracks, act as the bottom floor, includes the infrarred sensors and the slot for the battery. With everything set, it weighs not too far from a kilogram. There is a second slot for another battery, or for adding something heavy to add extra weight.

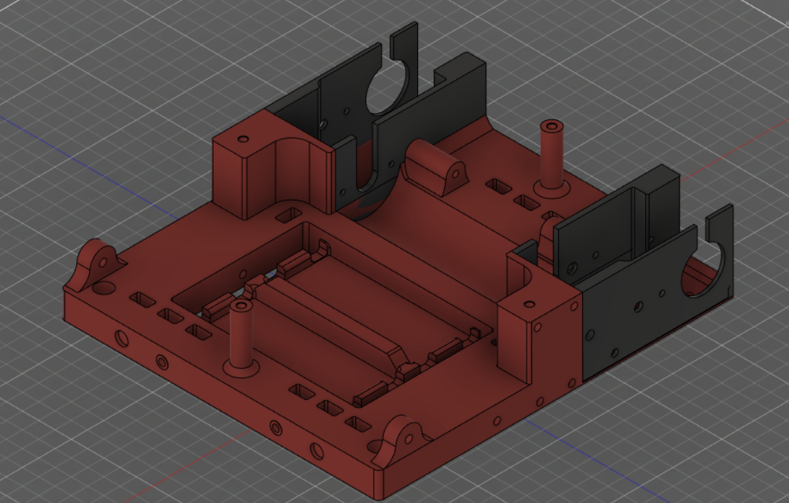
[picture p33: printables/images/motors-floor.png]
Motors-Floor


#### Electronics Floor
Second most important part, where almost all the electronics are located. This includes the PCB and the L298N motor driver, there are 2 slots, one for each. There are also some extra slots, intended for passing the wires through them. These are big because we wanted to save some material, reduce complexity in thinking how to properly distribute wires and easeness of installation.

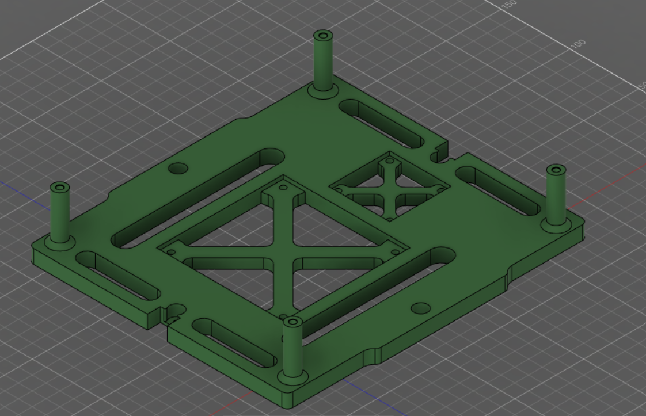
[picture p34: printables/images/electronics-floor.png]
Electronics-Floor


#### Top Layer
This layer serves only 3 purposes: decorative, sloting the power button and as a base for Rockins (explained below). The majority of shapes here are decorative and for saving some material.

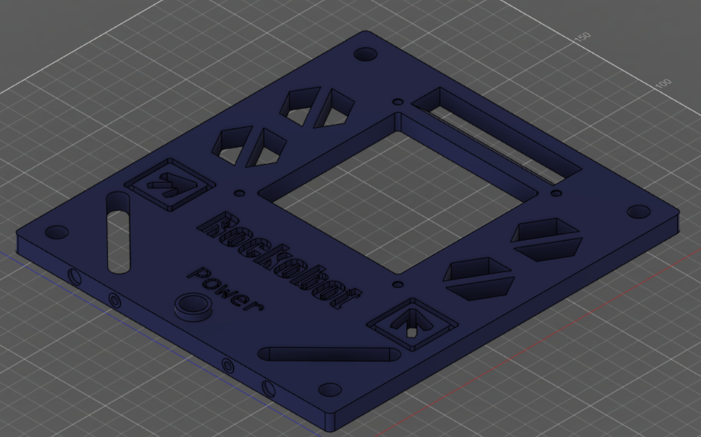
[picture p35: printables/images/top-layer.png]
Top-Layer


#### Rockins
The purpose of Rockins is to add a bit of modularity to Rockobot. In our case, we only added The Rock (Dwayne Johnson) head, who is the inspiration for the name of the robot. Rockins are made for adding some decorative pieces to the robot and changing them whenever you want, however, they can also be designed with some functionality, that's why we kept a big hole below in the Top Layer, to pass some wires through it, so we could also make a version with red LEDs in The Rock eyes.

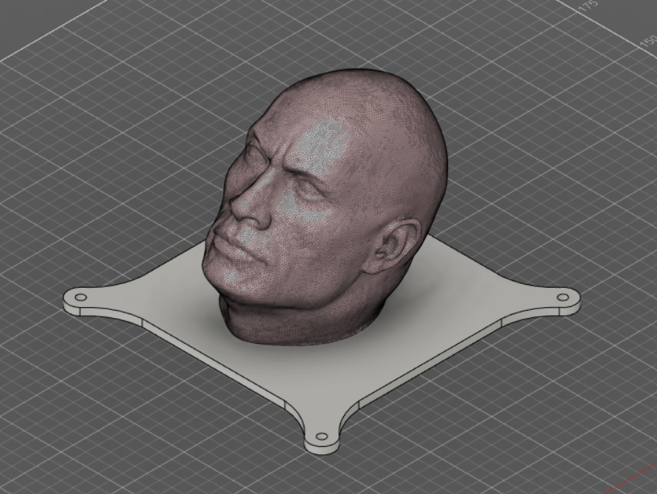
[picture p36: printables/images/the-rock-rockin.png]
Rockin-Rock


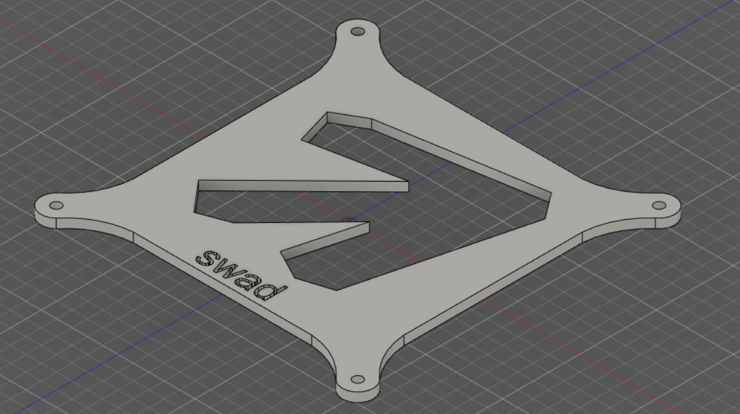
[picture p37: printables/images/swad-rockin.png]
Rockin-SWAD


### Rockobot Gearbox
Designed as a separate part, included to the Core design. Due to having 2 versions, (one independent to the core, the other is the integration) the Fusion 360 design is slightly messy. We recommend looking at the Adapted-To-Core version, which is more updated. There are various gears, a cylinder which represents the motor and the actual gearbox.

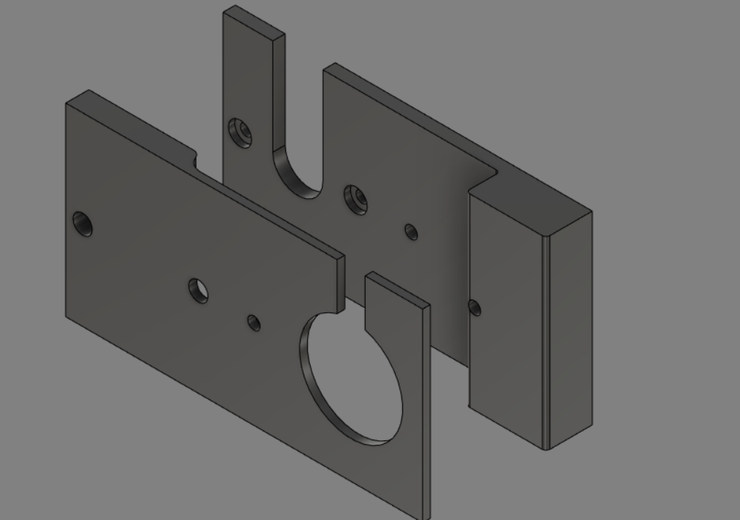
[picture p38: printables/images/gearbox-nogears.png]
GearBox-NoGears


### Rockobot Shield
Can be 3D printed, but it is designed to be done with a metal sheet and a laser cutter. The design includes some holes for screwing the US sensor, but we did not use them in the final design because it fitted exactly in the holes for the sensor. In Fusion we use 2 mm thickness, but we built it with 1 mm (we started getting to close to the 4 kg limit...) and also increased the curved ramp length a bit (about 20 mm). **Inox Steel 403** is the material used. Thanks to Pelochus' dad for actually doing this piece (we obviously did not have access to a laser cutter...). 

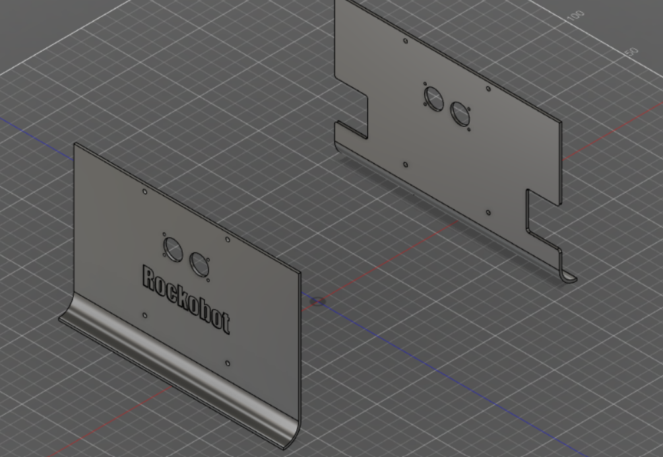
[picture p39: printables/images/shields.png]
Rockobot-Shield


### Outer Connector and Tracks
Extracted from a FPV Rover Tank from Thingiverse ([thanks to the guy who designed and published it](https://www.thingiverse.com/thing:1240754)). Both the track, outer connector and cogs where oversized by about 130% from the original design. There are also heavy modifications to the outer connector to adapt it to our design. The design is basically a simplified version of a real tank, in which the cogs apply the forces to the tracks and the outer connector serves as a structure to keep it all connected.

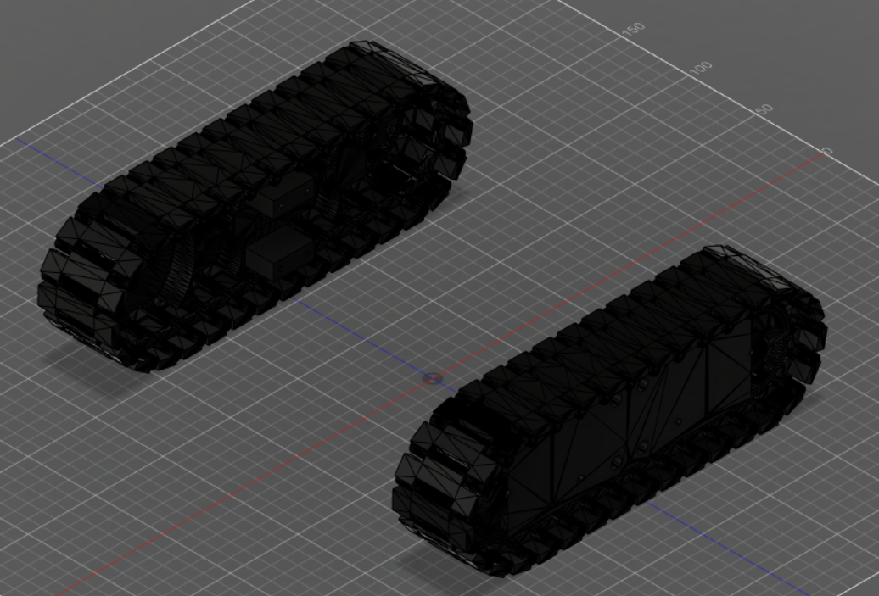
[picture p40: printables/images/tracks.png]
OuterConnector-Tracks


## Enhancing 3D prints strength
To enhance 3D prints strength, there are various techniques and slicer settings to adjust. These settings assume a **0.4 mm nozzle**, but it can be done with similarly sized nozzles. **Unless otherwise specified these are the common settings**:
- 215/250ºC Hotend and 60/75ºC Bed temperatures for PLA+/PETG respectively
- 50 mm/s speed, 60 mm/s for bigger parts, 40 mm/s for smaller, stronger parts.
- 4 walls, 0.4 mm thickness per wall
- Cubic/Cubic Subdivision/Grid Infill Type. We recommend (and used) cubic subdivision for strength in all axes and also to lower the amount of plastic used
- Avoid supports (it is possible, some parts may require higher fan speeds)
- Prints must be intelligently aligned with the axes so that the forces that will be applied are not ripping layers apart

| Part | Material | Fan  | Infill | Support | Ironing | Extras |
| --- | --- | ---- | --- | --- | --- | --- |
| Fillable Base | PLA+ | 25%  | 25% | No | No | |
| Motors Floor | PLA+ | 50%  | 15% | No | No | |
| Electronics Floor | PLA+ | 25%  | 10% | No | No | |
| Top Layer | PLA+ | 25%  | 10% | No | No | |
| The Rock Rockin | PLA+ | 100% | 5% | Yes | Yes | |
| Outer Connector | PLA+ | 25%  | 15% | No | No | |
| Cogs / Gears | PETG | 25%  | 100% | No | No | |

There were some TPU prints (tracks). The settings where these:
- 225ºC Hotend / 55ºC Bed
- 30 mm/s speed
- 3 walls, 0.4 mm thickness per wall
- Grid Infill Type / 10% infill. Infill can be changed if extra flexibility is desired.
- 80% Fan
- 0.16 mm layer height

It's worth mentioning that threaded inserts where used throughout the whole design. Using bare holes in 3D printing for screws is generally not a good idea,
that's why we decided to use threaded inserts, allowing better repairability and strength. They also require to have 1.6 mm walls, that is why that setting is 4 walls instead of the common 3 walls. Below there is a link in which CNC Kitchen explains how to design holes for 3D printable parts and threaded inserts.

## Mechanical designs
### Motor reduction through gears
Since we used two motors from an old VHS player, we had to reduce the speed of these. We incorporated a gearbox to the Motors Floor with various gears in it, achieving a **reduction of 85,75:1** (3.5<sup>3</sup> x 2). This way, we reduce our robot to a reasonable, controllable speed and we get **lots of extra torque**, which is critical for pushing (which is this robot's main purpose). The gearbox is adapted to both the Motors Floor, and to the Outer Connector and related pieces (the Main Cog that goes as the last gear was also from the guy who inspired our tracks).

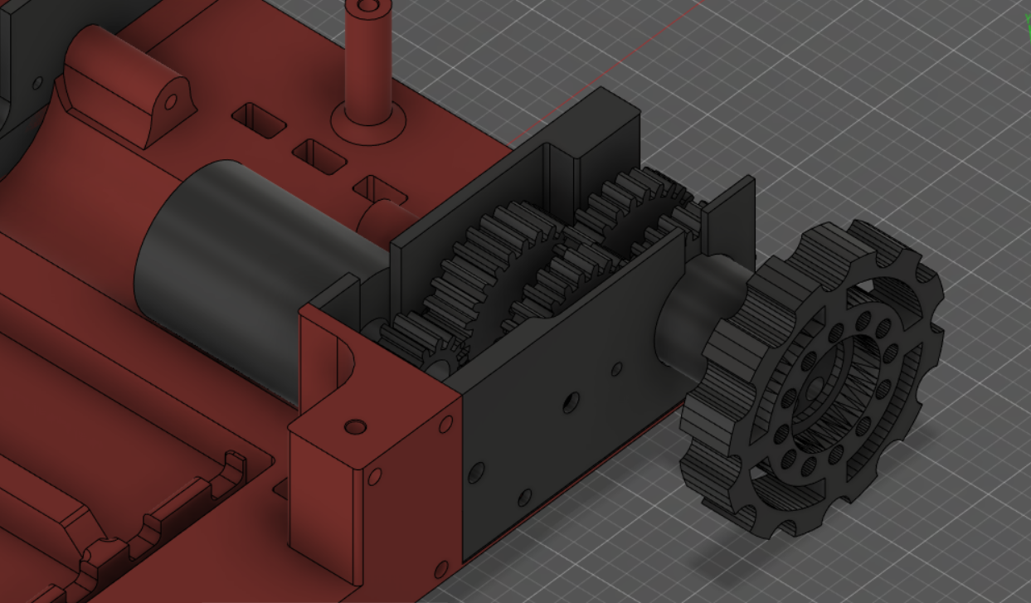
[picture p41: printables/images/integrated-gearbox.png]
GearBox implemented into the design


## Ideas
Some ideas for future revisions:
- Think about an easy way of adding weigh to the robot. This is in order to get as close as possible to the 4kg limit, without surpassing it before final design
- Reduce the number of screws and reduce the variety between them, for example, change the frontal MC to M3, to be the same as the back ones (or viceversa)
- Use more PETG and/or ABS/ASA. PETG is better for parts that require some give, flexibility and reduced friction (floors, guides). ABS/ASA is recommended for parts that need to be impact and heat resistant (gears, outer connectors). PETG has better layer adhesion.
- Redesign from zero if want lots of changes, because some sketches and other Fusion features are a bit messy
- Use more parametric dimensions
- Improve structure and think how to reduce filamente use along the way
- Think about a simpler version with wheels and 4 motors (as an alternative, speedier version, more than an upgrade) 

## Knowledge Base
- [Tank where the tracks design was extracted](https://www.thingiverse.com/thing:1240754)
- [3D printing Tricks](https://youtu.be/krrqydtneO0)
- [Designing for Threaded Inserts](https://www.cnckitchen.com/blog/tipps-amp-tricks-fr-gewindeeinstze-im-3d-druck-3awey)
- [Strengthening through texturing by CNC Kitchen](https://youtu.be/3-ygdNQThAs)
- [Transparent and strong PETG settings by CNC Kitchen](https://www.youtube.com/watch?v=9qb25Gi4Jv0)

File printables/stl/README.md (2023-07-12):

## STLs
All STLs needed for assembly are listed here. You will need at least one print of each file except for:
- All Rockins all optional
- FillableBase is not used in final design
- x64 Tracks
- x4 Lower Small Cog
- x4 Upper Small Cog
- x2 For every file in "gearbox" folder except for Gear2, which is x4

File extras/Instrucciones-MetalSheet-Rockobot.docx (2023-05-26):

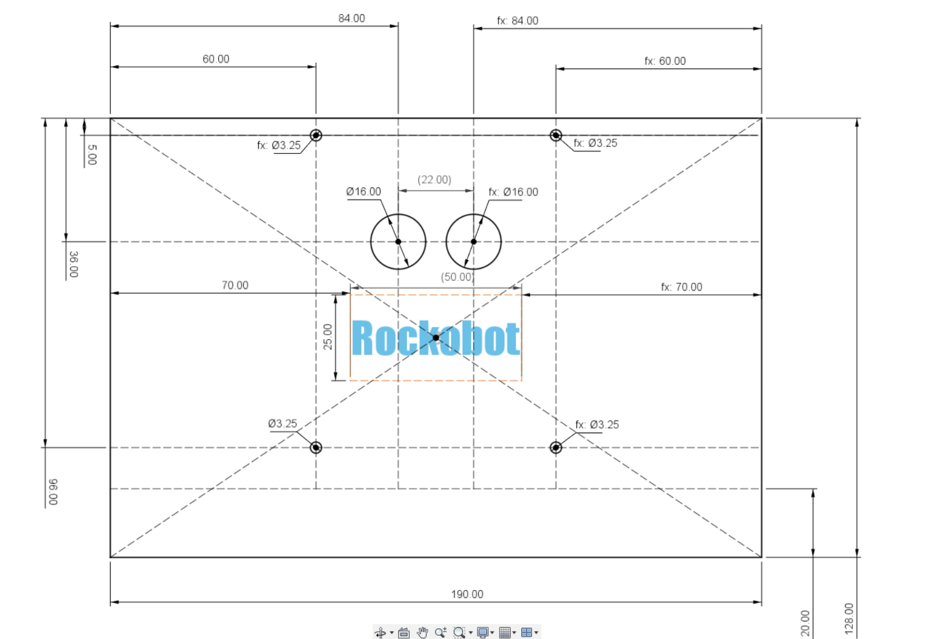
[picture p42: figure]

Sobre el diseño:

La línea discontinua horizontal de abajo (que esta a 20 mm de la última línea horizontal) es donde se aplicará el plegado con el diámetro de 25 mm (radio 12.5). La posición de las letras no importa mucho en altura, mientras este por debajo de los agujeros de 16 mm y por encima de los agujeros de 3.25 mm. Si deberán estar centradas en el eje vertical y utilizar la fuente Impact, además de poner la R en mayúscula (el resto en minúscula). Si es posible, aplicar un grabado para las letras, es decir, un quemado en el metal similar a un tatuaje en un humano. Si no, las letras deberán estar insertadas la mitad del grosor en la placa, es decir, si mide 2 mm, deberán tener una profundidad de 1 mm. Si tampoco es esto último posible, se puede recortar por completo (agujero completo con forma de las letras). El grosor de la placa será de 2 mm, si no se puede, de entre 1 y 2 mm lo más cercano a 2 mm.

Tras aplicar el plegado, el perfil y alzado (no se han dibujado los agujeros por simplicidad, ignorar la nota de grosor) deberán ser los siguientes:

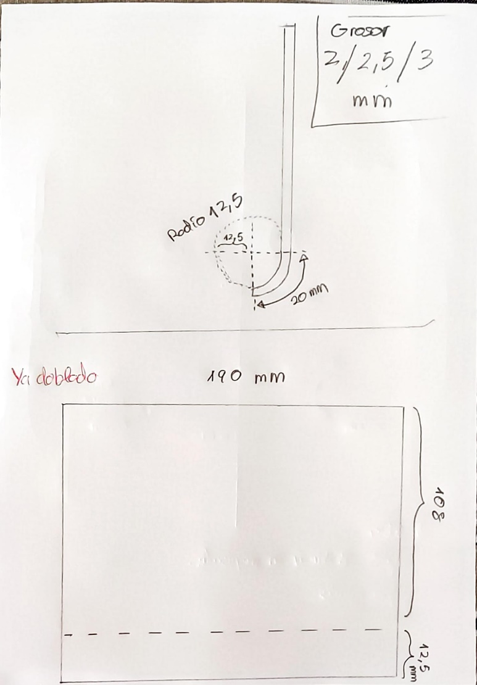
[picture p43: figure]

Estos serán los aspectos aproximados antes y después de doblar:

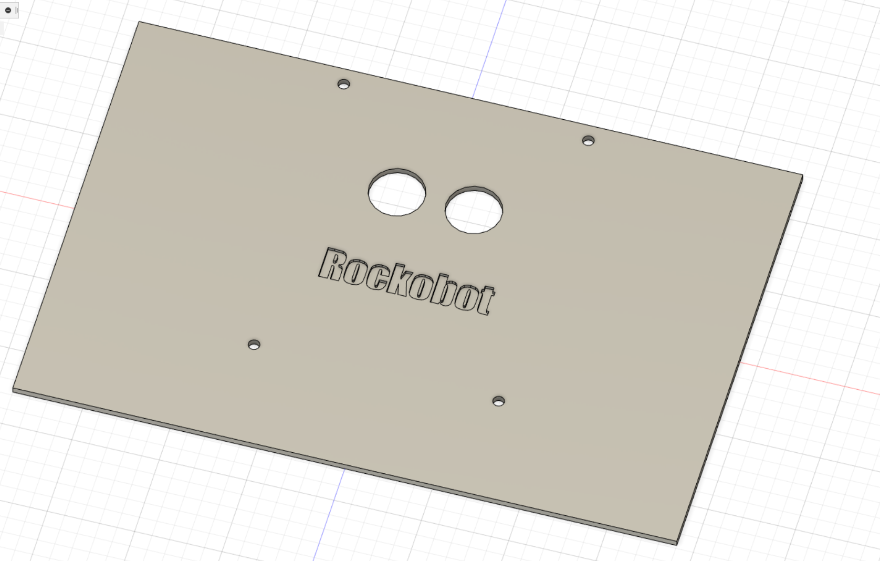
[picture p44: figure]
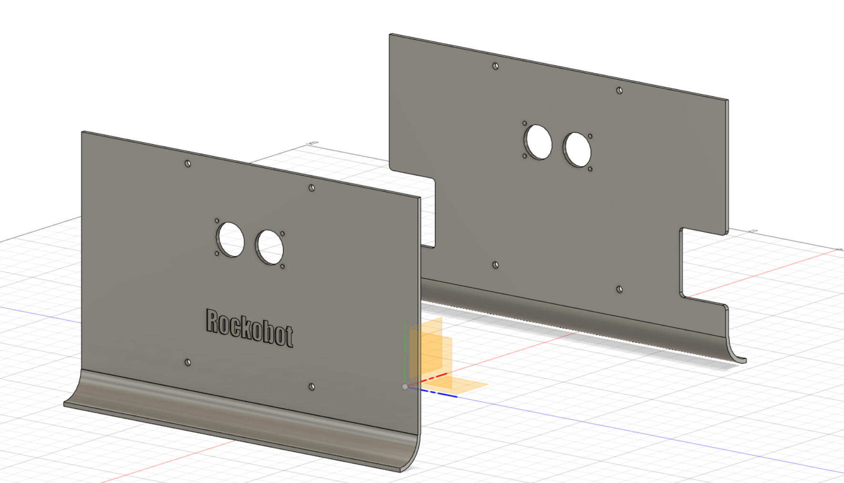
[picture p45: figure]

Por último, hacer una segunda placa exactamente igual, pero con estos añadidos:

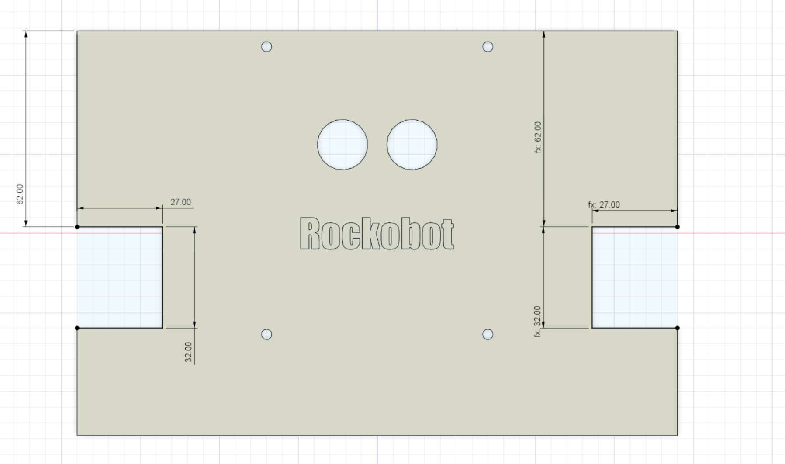
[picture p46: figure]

Si es posible redondear las esquinas, tanto las vistas en este nuevo añadido como las esquinas previas.

Última nota: Se puede extender la longitud más allá de la línea discontinua, pero se debe aplicar la curvatura en el mismo lugar, es decir a 20 mm de la línea original final. Esto sirve para conseguir que la forma de pala sea más grande y por tanto más útil su propósito de levantar enemigos. Consultar con Raimundo.

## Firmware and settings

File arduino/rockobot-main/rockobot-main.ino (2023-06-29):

/**
 * rockobot-main.ino
 *
 * Arduino code for Rockobot
 * More information: https://github.com/Pelochus/rockobot/tree/main/arduino
 *
 * Authors:
 *   Pelochus
 *   Jose-HH
 */

#include <HCSR04.h> // RCWL-1601 is compatible
#include <L298N_Rockobot.h>

// See PCB/Schematics for pin numbers
#define ENA 3
#define IN1 4
#define IN2 5
#define IN3 6
#define IN4 7
#define ENB 9

#define TRIGGER 10
#define ECHO_FRONT 11
#define ECHO_BACK 12

#define IR_BACK A0
#define IR_RIGHT A1
#define IR_LEFT A2
#define IR_FRONT A3

// General constants
const uint16_t FULL_POWER_THRESHOLD = 8000; // After 8 seconds, always use full power
const uint16_t STARTUP_DELAY = 3000; // 3 seconds mandatory delay for competition
const uint8_t ACTION_DELAY = 50; // Delay in ms between one full loop and next loop

// IR and danger zone related constatns
const uint16_t IR_THRESHOLD = 300; // If higher than this, we are entering danger zone (out of ring)
const uint8_t STUCK_COUNT = 25; // If we reach STUCK_COUNT loops detecting black lines, we are stuck, change direction
const uint8_t TURN_CYCLES = 700 / ACTION_DELAY + 1; // Loops required for 90º rotation at 100% speed (We calculated 700 ms 90 deg at 16.7V battery)

// US and Search related constants (values in cm)
const uint8_t DIRECTION_CHANGE_THRESHOLD = 5; // If difference between sensors is higher than this, change direction while searching
const uint8_t US_NEARBY_ENEMY = 30;
const uint8_t FULL_POWER_NEAR_ENEMY = 12;
const uint8_t MAX_DISTANCE = 150; // Ring dimensions = 160 x 65. Diagonal distance = 170 mm

uint16_t extra_delay = 0;
uint16_t initial_time = 0;
uint16_t current_time = 0;
uint8_t front_counter = 0;
uint8_t back_counter = 0;
uint8_t search_stage = 0;

UltraSonicDistanceSensor us_front(TRIGGER, ECHO_FRONT, MAX_DISTANCE);
UltraSonicDistanceSensor us_back(TRIGGER, ECHO_BACK, MAX_DISTANCE);
L298N_Rockobot driver(ENA, ENB, IN1, IN2, IN3, IN4);

// Structure: 
// First read values from sensor, then think what to do and send info to motors
void rockobot_think() {
    extra_delay = 800; // Add an extra delay when encountering black lines

    ////////////////
    // Read Sensors
    ////////////////
    uint8_t front_distance = us_front.measureDistanceCm();
    uint8_t back_distance = us_back.measureDistanceCm();
    bool ir_front = (analogRead(IR_FRONT) > IR_THRESHOLD);
    bool ir_back = (analogRead(IR_BACK) > IR_THRESHOLD);
    bool ir_right = (analogRead(IR_RIGHT) > IR_THRESHOLD);
    bool ir_left = (analogRead(IR_LEFT) > IR_THRESHOLD);

    /////////
    // Think
    /////////
    uint8_t speed = 100;
    direction_t direction = driver.get_direction(); // Maintain same path while thinking

    // Anti-ramp
    if ((ir_front ? 1 : 0) + (ir_back ? 1 : 0) +
        (ir_right ? 1 : 0) + (ir_left ? 1 : 0) > 2) {
        direction = RIGHT;
    }
    else if (ir_front) {
        direction = BACKWARD;

        if (front_counter > STUCK_COUNT) {
            direction = RIGHT;
            front_counter /= 2;
        }

        front_counter++;
        back_counter = 0;
    }
    else if (ir_back) {
        direction = FORWARD;

        if (back_counter > STUCK_COUNT) {
            direction = RIGHT;
            back_counter /= 2;
        }

        front_counter = 0;
        back_counter++;
    }
    // We want even higher delays on rotations, because robot is slower with only one motor
    else if (ir_right) {
        extra_delay += 200;
        direction = WIDE_LEFT;
    }
    else if (ir_left) {
        extra_delay += 200;
        direction = WIDE_RIGHT;
    }
    else {
        ///////////////////////////////////////////////////////
        // Not in danger zone, search and target enemy with US
        ///////////////////////////////////////////////////////
        extra_delay = 0; // Reset delay if not in danger
        speed = 80;

        int16_t us_diff = front_distance - back_distance; // If negative, back_distance is farther from something and viceversa
        uint8_t us_min = (front_distance < back_distance) ? front_distance : back_distance;
        bool search = us_min > US_NEARBY_ENEMY; // Decide whether to skip or not search stage

        //////////
        // Search
        //////////

        if (search) {
            switch (search_stage) {
                case 0 ... (TURN_CYCLES - 1):
                    direction = RIGHT;
                    break;
                case 2 * TURN_CYCLES ... (3 * TURN_CYCLES):
                    direction = LEFT;
                    break;
                default:
                    direction = FORWARD;
            }

            search_stage++;
            search_stage %= 4 * TURN_CYCLES;
        }

        ////////////////
        // Target enemy
        ////////////////

        if (abs(us_diff) > DIRECTION_CHANGE_THRESHOLD && us_min < US_NEARBY_ENEMY) {
            if (us_diff > 0) direction = BACKWARD;
            else if (us_diff < 0) direction = FORWARD;
            // else will retain current direction
        }

        // Activate max power if close enough
        if (us_min < FULL_POWER_NEAR_ENEMY) speed = 100;
    }

    //////////////////////
    // Act after thinking
    //////////////////////

    driver.set_speed_percentage(speed);
    driver.set_direction(direction);
}

void setup() {
    // Both Motors and US sensors pinModes are set inside their respective classes
    pinMode(IR_FRONT, INPUT);
    pinMode(IR_BACK, INPUT);
    pinMode(IR_RIGHT, INPUT);
    pinMode(IR_LEFT, INPUT);

    driver.set_speed_percentage(0);
    delay(STARTUP_DELAY); // Mandatory delay for official competition
    initial_time = millis();
}

void loop() {
    rockobot_think();

    // Overwrite speed always to 100% if combat takes too long
    // This also allows getting to full speed if we are in a pushing struggle and
    // the enemy is short enough that the US sensor doesn't activate full power
    current_time = millis();
    if (current_time - initial_time > FULL_POWER_THRESHOLD) {
        driver.set_speed_percentage(100);
    }

    delay(ACTION_DELAY + extra_delay);
}

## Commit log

2023-04-06 Added info about TPU prints
2023-05-12 Added KiCad project, including PCB, schematics and gerber
    [rockobot-B_Cu.gbl, rockobot-B_Mask.gbs, rockobot-B_Paste.gbp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]
2023-05-12 Create gerber README.md
2023-05-12 Updated Arduino file
2023-05-13 Updated schematic with pin info about L298N driver
    [rockobot.kicad_sch]
2023-05-13 Fixed comment in schematic
    [rockobot.kicad_sch]
2023-05-30 Updated Arduino code
2023-06-25 Added new minor features, like full power after some time
2023-06-25 Modified main algorithm to avoid traps
    [rockobot-main.ino]
2023-06-26 Added gearbox reduction info
2023-06-26 Final version before tournament + fix
    [rockobot-main.ino]
2023-06-29 Fixed tabs and spaces
    [rockobot-main.ino]
2023-06-29 Added final assembly photo
2023-07-12 Added stl and design files
    [ElectronicsFloor.stl, FillableBase.stl, Gear1.stl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]
2023-07-12 Added outer connectors STLs
    [OuterConnectorLeft.stl, OuterConnectorRight.stl]
2023-10-14 Added Arduino Blog link
2023-10-14 Fix Arduino link
